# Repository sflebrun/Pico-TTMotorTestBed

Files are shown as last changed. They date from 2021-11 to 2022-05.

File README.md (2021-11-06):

# Pico-TTMotorTestBed
Environment and Code for testing two DC TT Gear Motors using a TB6612FNG Dual H-Bridge module and a Pico

## Build Environment
The code for ths project was developed using Visual Studio Code.  I see no reason why Thonny cannot be used with the code.

### Visual Studio Code modifications

* Add to the settings.json file the following line:<br/>
  "python.analysis.extraPaths:" ["./."]
  * This allows the editor to import from local files.
* Recommended (**Required**) Extensions:
  * MagicPython
  * **Pico-Go**
  * Pylance
  * Python

### Pico
The MicroPython UF2 file needs to be uploaded to the Pico.  This is the real program running on the Pico and it interrupts the
python code.  The three class files, ButtonInfo.py, MotorControl.py, and TTMotor.py must be uploaded to the Pico before the main
code, TTMotorTestBed.py, can run.

On multiple occasions, when trying to run the TTMotorTestBed python code, an error would occur that it could not find TTMotor.
Running the program again resolved this problem.  I do not know if this is a Pico issue or a Visual Studio Code/Pico-Go issue.

## Parts List
The links are places where I have bought the parts.  They are intended as recommendations and so you can 
identify the parts.

* [Raspberry Pi Pico](https://www.seeedstudio.com/Raspberry-Pi-Pico-p-4832.html)
* [TB6612FNG Dual H-Bridge](https://www.amazon.com/dp/B08J3S6G2N?psc=1&ref=ppx_yo2_dt_b_product_details&pldnSite=1)
* [2 TT Gear Motors with Wheels](https://smile.amazon.com/dp/B098Q1BCX5?psc=1&ref=ppx_yo2_dt_b_product_details)
* [Breadboard -- 830 points](https://smile.amazon.com/DEYUE-Solderless-Prototype-Breadboard-Points/dp/B07NVWR495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)
* [Dupont connector, male to male, various lengths](https://smile.amazon.com/Elegoo-EL-CP-004-Multicolored-Breadboard-arduino/dp/B01EV70C78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)
* [2 Breadboard Potentiometers](https://smile.amazon.com/dp/B09G9TBY38?psc=1&ref=ppx_yo2_dt_b_product_details)
* [3 Breadboard Push Buttons](https://smile.amazon.com/dp/B07XF3YMJ4?psc=1&ref=ppx_yo2_dt_b_product_details)
* 3D Printed Motor Stand [optional] See File: **Dual TT Gear Motor Test Bed.stl**
* 4 M3x30mm screws and nuts, if 3D Printed Motor Stand is used.

**Note** These are the parts that I used.  You can substitute most of the parts with something equivalent.  If you substitute a different
microcontroller board for the Pico or another Dual H-Bridge module for the TB6612FNG, changes to the code will be necessary.  For the Dual
H-Bridge Module see the comment about the Standby Pin in the MotorControl.py file.

## 3D Printed Parts
There is only one part that needs to be 3D printed.  That is the **Dual TT Motor Test Bed.stl**.  This can be printed with PLA filament with layers
set to 0.2mm and 20% infill.  No supports are necessary.  My printer is an Ender 3 Pro and the test bed had to be rotated 45 degrees so that the
test bed would fit in the 220mm x 220mm build area.

The TT Gear Motors mount on the pair of walls and requires M3 screws with nuts.  I recommend 30mm length screws. The screws pass through two walls
that are 25mm apart measured by the outside of each wall.  A 26mm length screw might work though it may not have enough thread sticking out to hold
the nut securely.

The Cad file for the TT Gear Motor Mount is included as **TestBedForTwoMotorsV3.FCStd**.  This file is a FreeCad file.

## The Code

### The Main Python Program

The main file, that contains the infinite loop, is **TTMotorTestBed.py**.  I ran this program thought the Pico directly from Visual Studio Code.
Clicking the ***Run*** button on the lower status line causes VS Code to upload the file and run it.  The extension ***Pico-Go*** provides the Run and upload 
buttons on the GUI.  This method of running the code means that I manually started and stopped running the Python code.

If the file **TTMotorTestBed.py** is renamed to **main.py** and uploaded to the Pico, the MicroPython interrupter program will automatically read and
run it everytime the Pico is powered up.

### Interrupt Handling

There are two push buttons used to toggle the directions of the motors.  One button per motor.  The code uses interrupts to handle the button being pushed.
Multiple issues had to be handled during the development of the code.  The first was button bounce and the other was that the Pico does not handle 
interrupts immediate and schedules them to be processed.

#### Debouncing

When a push button is pressed and released, it seldoms makes and breaks the connection cleanly.  Instead, the signal received from the pin may have a 
series of rises and falls in a small window of time as the connection is made and broken.  This is  called bounce.

There are two ways to handle debouncing: hardware solutions and software solutions.  The hardware solution is the better of the two solutions and 
should be used in production level electronics.  The con of this method is that it adds more components to the breadboard in a capacitor and a couple 
of resisters per button.  The software solution usually involves examining the button over a small window of time until it stablizes.  The con of
this solution is that if you make your window too small, you get false readings.

Because this is a one-off project and built on a single breadboard, I choose to use a software solution.  An additional factor needed to be considered
with my software solution [See the function ***buttonDebounce()*** in **TTMotorTestBed.py**].  The problem is that bounce can occur on both the push 
and release of a button.  The interrupt is only intended to trigger a direction toggle on the push or rising edge of the signal.  To over come the
fact that the falling edge can bounce and therefore look like another rising edge, the debounce function ignores the state of the button pin.
Instead, it looks for the state to remain the same over a specified period of time.  Once the button has stablized, the final state of the button
is used.  If the pin value is High, the interrupt function handles the interrupt.  If the final state is low, the interrupt ignores the interrupt.

#### Delayed Interrupt Handling

Normally when writing an interrupt handler, two things are considered.  The fist is to keep the interrupt handler as short, timewise, as possible.
The second is to disable additional interrupts for the same event from occurring while the first interrupt is being handled.  On the Pico, it is
not possible to prevent multiple interrupts from occurring with the same event.  In the case of the push button with bounce, each time the signal
rises another interrupt is generated.  In other words, multiple interrupts can be generated due to button bounce in the time between the first
interrupt occurs and when it is handled.  Disabling new interrupts during the processing of the interrupt handle fails to work in this case because
the extra interrupts have already occurred.

The debounce function handles most of the cases of multiple interrupts.  The one exception is if the button is held down for a long enough period
of time and multiple interrupts are queued for processing.  In this case, the interrupt handler processes the first interrupt and the pin value is HIGH.  When 
the second interrupt is handled, the interrupt handler finds that the button value is still HIGH and treats it as a new interrupt.  This case is 
resolved in the code by requiring a second interrupt that detects the release of the button.  Only one rising interrupt will be processed until a
matching falling interrupt is detected.  So if there are multiple rising or button pressed interrupts detected, all secondary interrupts are ignored 
until the button is released and the falling interrupt is detected.

* [See Interrupt Handling Problem in Pico -- Raspberry Pi Forums](https://forums.raspberrypi.com/viewtopic.php?t=319655) for more details.

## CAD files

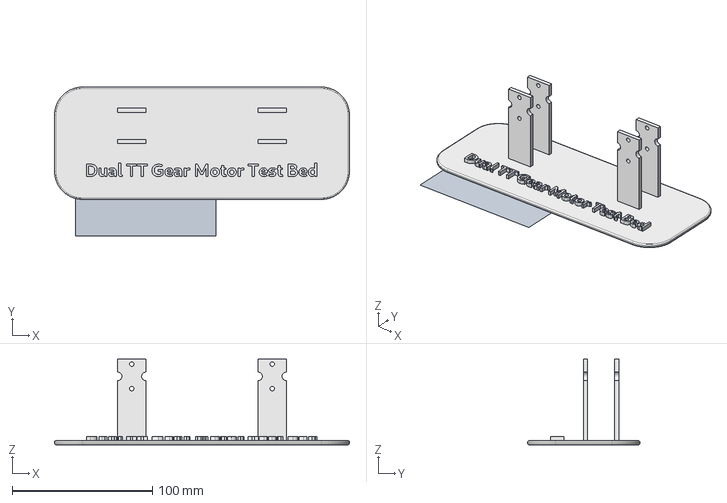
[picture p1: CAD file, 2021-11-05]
3D Models/TestBedForTwoMotorsV3.FCStd
210.0 x 106.0 x 61.0 mm
WPProxy
Dual TT Gear Motor Test Bed

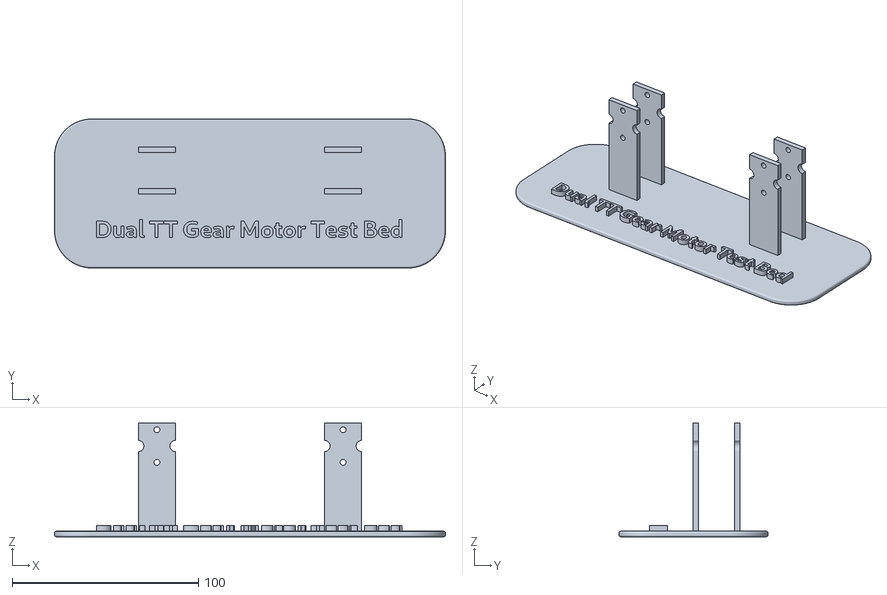
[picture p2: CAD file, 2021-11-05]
3D Models/Dual TT Gear Motor Test Bed.stl
210.0 x 80.0 x 61.0

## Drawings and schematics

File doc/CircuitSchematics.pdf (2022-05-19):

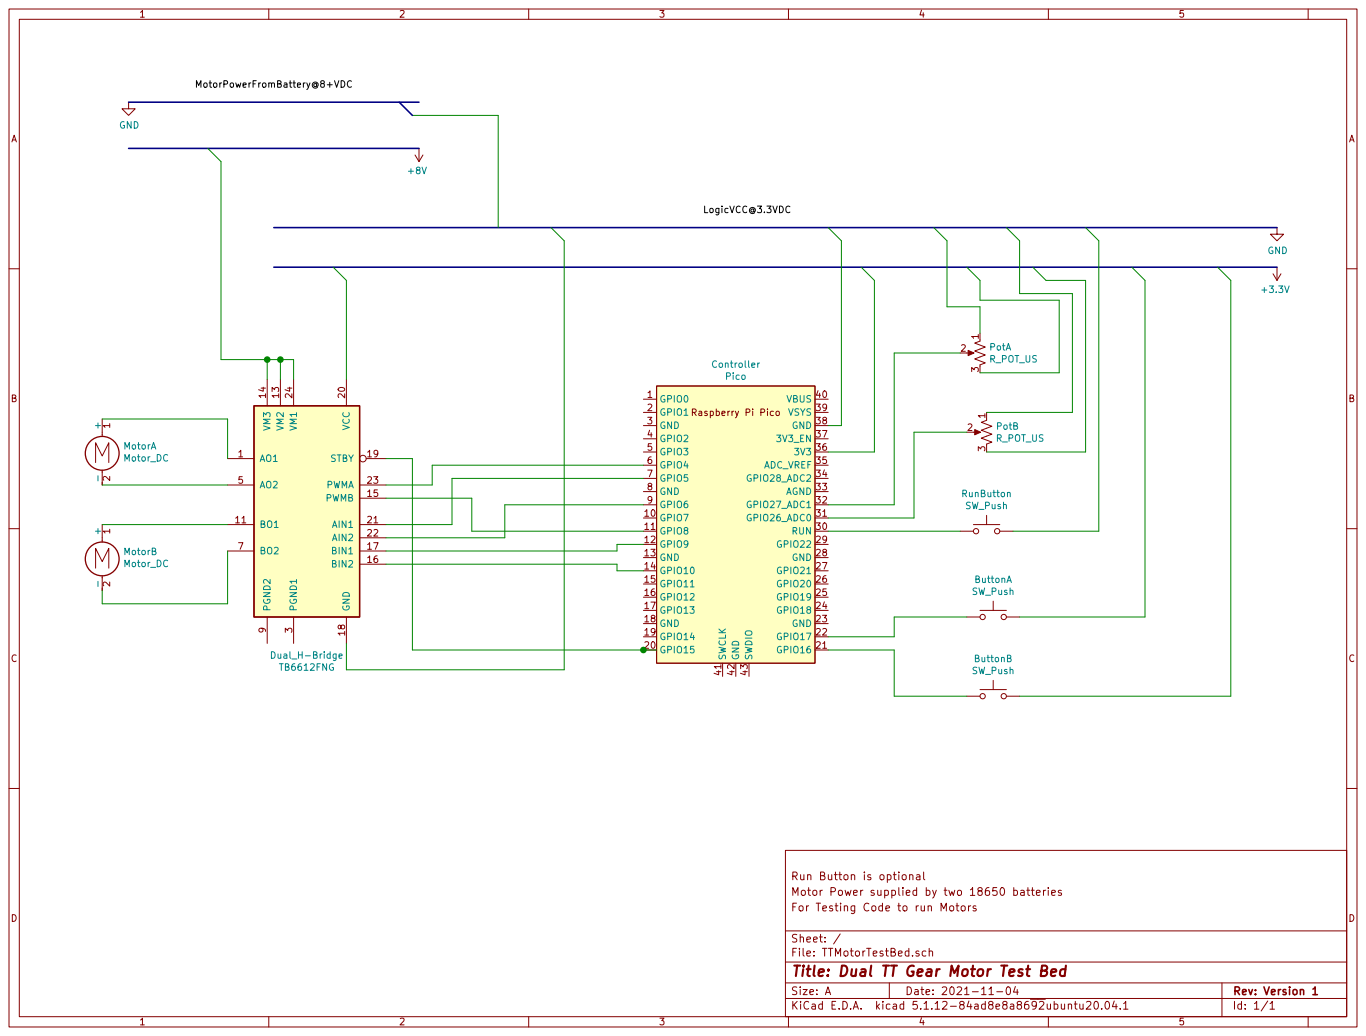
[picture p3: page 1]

3 PotB R_POT_US Raspberry Pi Pico GPIO0 1 GPIO7 10 GPIO8 11 GPIO9 12 GND 13 GPIO10 14 GPIO11 15 GPIO12 16 GPIO13 17 GND 18 GPIO14 19 GPIO1 2 GPIO15 20 GPIO16 21 GPIO17 22 GND 23 GPIO18 24 GPIO19 25 GPIO20 26 GPIO21 27 GND 28 GPIO22 29 GND 3 RUN 30 GPIO26_ADC0 31 GPIO27_ADC1 32 AGND 33 GPIO28_ADC2 34 ADC_VREF 35

Run Button is optional
Motor Power supplied by two 18650 batteries
File: TTMotorTestBed.sch Sheet: / For Testing Code to run Motors

Id: 1/1 Title: Dual TT Gear Motor Test Bed

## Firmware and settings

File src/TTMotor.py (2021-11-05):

# Defines the class that represents one motor part of TB6612FNG Dual H-Bridge.
#
# Note: This class is actually independent of what type of DC Motor is attached to 
#       the Dual H-Bridge Module.  My test setup is for a pair of TT Gear Motors,
#       hence the name.
#
# Three pins control each motor -- PMW, IN1, and IN2.  
#
# Motors are labeled A and B on the H-Bridge module.  This class only deals with
# a single motor so the A and B labels are ignored.  See the MotorControl class 
# for dealing with both motors and the Standby Pin.

from machine import Pin, PWM

# This class represents the part of the Dual H-Bridge module.
class TTMotor:
    """A Class that contains the state of a DC Motor, primarily for TT Gearbox Motors"""

    # Constants that denote motor direction.
    # Should be constants but Python const() does not appear to work in MicroPython
    # Please do no change these variables.
    STOPPED   = 0
    FORWARD   = 1
    BACKWARD  = 2

    # Default Constructor
    #    Current Direction is none or STOPPED
    #    Next Direction is FORWARD (by setting previous Direction to BACKWARD)
    #
    # @param  gpioPWM   The GPIO Pin Number, not the physical pin number, of the
    #                   pin used to set the motor speed with a pulse width modulation
    # @param  gpioIN1   The GPIO Pin Number used to determine direction of motor in
    #                   conjunction with gpioIN2
    # @param  gpioIN2   The GPIO Pin Number used to determine direction of motor in
    #                    conjunction with gpioIN1
    #
    def __init__(self, gpioPWM: int, gpioIN1: int, gpioIN2: int ):
        self.gpioPWM = gpioPWM
        self.gpioIN1 = gpioIN1
        self.gpioIN2 = gpioIN2
        self.motorSpeed  = 0
        self.IN1Value = False
        self.IN2Value = False

        if ( gpioPWM < 0 ):
            # Invalid value
            raise ValueError("TTMotor Constructor: Invalid GPIO PWM Pin number: " + str(gpioPWM))
        else:
            #Initialize the PWM pin
            self.pinPWM = Pin(gpioPWM, mode=Pin.OUT)

            self.pwmPin = PWM(self.pinPWM)
            self.pwmPin.freq(10000)  # 10kHz
            self.pwmPin.duty_u16(0)  # off

            # Initialize the two signal input pins
            self.in1    = Pin(gpioIN1, mode=Pin.OUT)
            self.in2    = Pin(gpioIN2, mode=Pin.OUT)

            self.in1.low()
            self.in2.low()

        self.currentDirection  = self.STOPPED
        self.previousDirection = self.BACKWARD

 
    # Determine if Pin ID is one of the GPIO Pins associated with this motor
    def usesPin( self, pinID: int ):
        if ( pinID == self.gpioPWM or pinID == self.gpioIN1 or pinID == self.gpioIN2 ):
            return True
        else:
            return False
        


    # Return the configured GPIO Pin object
    def pwm(self):
        return self.gpioPWM

    # Returns the GPIO Pin object for IN1
    def signal1Pin(self):
        return self.in1

    # Returns the GPIO Pin object for IN2
    def signal2Pin(self):
        return self.in2

    # Returns what the IN1 Pin should be set to: True == HIGH, False == LOW
    def signal1(self):
        return self.IN1Value

    # Returns what the IN2 Pin should be set to: True == HIGH, False == LOW
    def signal2(self):
        return self.IN2Value

    # Returns the Current Direction
    def direction(self):
        return self.currentDirection

    # Returns what the current speed is set to
    def speed(self):
        return self.motorSpeed
     
    # Returns the Next Direction
    #
    # The the toggle sequence is FORWARD --> STOPPED --> BACKWARD --> STOPPED --> repeat
    # So the next direction refers to the next N0N-Stopped direction.
    def nextDirection(self):
        if ( self.previousDirection == self.BACKWARD ):
            return self.FORWARD
        else:
            # all other values for Previous Direction leads to 
            return self.BACKWARD

    # Change direction based on the last none-stopped direction
    # Toggle Cycle:  FORWARD --> STOPPED --> BACKWARD --> STOPPED --> repeat
    def toggleDirection(self):
        if ( self.currentDirection == self.STOPPED ):
            # If currect direction is STOPPED, use the previous (non-STOPPED) direction
            # to determine the new current direction.
            if ( self.previousDirection == self.BACKWARD ):
                self.currentDirection = self.FORWARD
            else:
                self.currentDirection = self.BACKWARD
        else:
            # If current direction is FORWARD or BACKWARD, new current direction is STOPPED
            # and new previous direction is set to the old current direction
            self.previousDirection = self.currentDirection
            self.currentDirection  = self.STOPPED

    # Set actual Motor Speed and Direction
    #
    # This function actually writes to the Dual H-Bridge module, hence causing the motors to 
    # turn or to stop.
    def  motorControl( self, speed ):
        signal1 = False
        signal2 = False

        # Set Motor Speed to the passed value which may not match the zero speed of STOPPED
        # but it does match the Potentiometer that determines the moving speeds.
        self.motorSpeed = speed

        #print("Current Direction = ", self.currentDirection)
        if ( self.currentDirection == self.FORWARD ):
            signal2 = True
        elif ( self.currentDirection == self.BACKWARD ):
            signal1 = True
        else:
            speed = 0

        # Set Direction: STOPPED, FORWARD, or BACKWARD
        self.IN1Value = signal1
        if ( signal1 ):
            self.in1.on()
        else:
            self.in1.off()

        self.IN2Value = signal2
        if ( signal2 ):
            self.in2.on()
        else:
            self.in2.off()

        ## Set Speed
        self.pwmPin.duty_u16(speed)

        # End of MotorControl()


        
        

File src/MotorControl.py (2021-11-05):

# Class to handle two motors on a single TB6612FNG Dual H-Bridge module
# plus the extra control pins on the module, namely the STANDBY Pin.
#



from machine import Pin

import TTMotor

# The TB6612FNG Dual H-Bridge control class.
#
# The addition of the Standby Pin makes this class specific to the
# TB6612FNG module.  Removing all references to the Standby Pin would
# make this a generic Dual H-Bridge Controller class
#
class MotorControl:
    """Class to manage two TTMotor objects connected to the same
    TB6612FN Dual MOSFET H-Bridge module."""

    # Primary Constructor for this Class
    #
    # Note: It is the responsibility of the caller to have already created
    #       TTMotor objects for each of the two motors.  Only one motor is
    #       actually required if two motors are not connected to the H-Bridge.
    #
    # @param standby  The GPIO Pin Number, not the physical pin number, of the
    #                 pin used to control the StandBy pin on the TB6612FNG module.
    #
    # @param frontMotor  The TTMotor object for the motor that is considered to be
    #                    at the front of the car.
    #
    # @param backMotor   The TTMotor object for the motor that is considered to be
    #                    at the back of the car.
    #
    # @param flag        A boolean flag that denotes if True that the motors turn CW 
    #                    (Clockwise) when moving forward and if False that the motors
    #                    turn CCW (Counter Clockwise) when moving forward. 
    #                    NOT IMPLEMENTED YET -- Might be implemented when using four
    #                    motors and two TB6612FNG Dual H-Bridge modules.
    def __init__( self, standby: int, frontMotor=None, backMotor=None):
        self.gpioSTANDBY = standby
        self.pinSTANDBY  = Pin( self.gpioSTANDBY, mode=Pin.OUT )
        self.motors      = {}

        # Offsets for the Front and Back Motors in the motors array
        self.FRONT = 1
        self.BACK  = 2

        if ( frontMotor != None ):
            self.motors[self.FRONT] = frontMotor

        if ( backMotor != None ):
            self.motors[self.BACK]  = backMotor

        self.pinSTANDBY.high()

    # There is no general way to obtain the ID used to create a Pin object
    # after it has been created.  The following is a HACK, that assumes that
    # when a Pin object is converted to a string "Pin(xx, yy==zz, gg=pp)"
    # that the first parameter after the "(" starts in offset [4] and 
    # ends with a comma.
    def getPinID( self, pin ):
        pinString = str(pin)
        pinData   = pinString[4:-1].split(",")
        return int(pinData[0])


    # Modify speed being written to the each of the wheels
    # Either use speed or {frontSpeed and backSpeed}
    # If either frontSpeed or backSpeed are set to 0 or greater, those speeds
    # are used for each motor.  If they are not set, speed is used.  If none
    # of them are set, the speed used is 0.
    #
    # NOTE: This will result in data being written to the H-Bridge module and
    #       the motors to physically change speed.
    #
    def changeSpeed( self, speed=-1, frontSpeed=-1, backSpeed=-1):
        # Determining actual speeds based on which speed parameters are set or
        # in are their default values.
        if ( speed < 0 ):
            speed = 0

        if ( frontSpeed < 0 ):
            frontSpeed = speed

        if ( backSpeed < 0 ):
            backSpeed = speed

        # Make sure speeds are not greater than maximum value: 0xFFFF == 65535
        frontSpeed = frontSpeed & 0xFFFF
        backSpeed  = backSpeed  & 0xFFFF

        # change Motor Speeds
        #
        # NOTE: If TTMotor object was None, the if statements will evaluate to False
        if ( self.FRONT in self.motors.keys() ):
            self.motors[self.FRONT].motorControl(frontSpeed)

        if ( self.BACK  in self.motors.keys() ):
            self.motors[self.BACK].motorControl(backSpeed)


    # Toggle the direction the motor should turn based on Pin Number
    def toggleDirection(self, gpioPWM: int ):
        print("Toggle Direction on PWM Motor: ", gpioPWM)

        # Loop through motors array and toggle the direction on the appropriate motor
        for motor in self.motors.values():
            if ( motor.usesPin( gpioPWM ) ):
                motor.toggleDirection()
                print("Toggle Direction: Motor ID: ", gpioPWM, ", Direction = ", motor.direction())
        

    #
    # End of MotorControl class
    #

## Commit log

2021-11-05 Add files via upload
    The PDF is the schematic drawing of my setup. The stl and FCStd are the 3D model for the stand that holds the two motors. Initial checkin.
    [Dual TT Gear Motor Test Bed.stl, TestBedForTwoMotorsV3.FCStd]
2021-11-05 Add files via upload
    Initial checkin for source code. Note: TTMotorTestBed.py is the main program file. It can be run manually or renamed to main.py, loaded onto the Pico, and run automatically when the Pico powers up.
2021-11-05 Add files via upload
    Missed a file during initial commit. This file contains the class that manages a single DC Motor that is connected through a Dual H-Bridge module.
    [TTMotor.py]
2021-11-05 Added second interrupt handler. The original handler is for rising signal interrupts which occur when a button is pressed. The new handler is for falling signal interrupts which occur when a button i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
    The new behavior is that once a pressed button interrupt has been handled, the code will ignore all other pressed interrupts
    until a released button interrupt has occurred. There is bounce occurring when the button is pressed and released. This
    prevents secondary pressed button interrupts that occur after the first one is detected and before the first one is processed
    from triggering false detection. Again this is due to bounce and the fact that the Pico does not process an interr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
    [ButtonInfo.py, TTMotorTestBed.py]
2021-11-05 Moved files into subdirectories for Documentation, 3D Printing, and Source
    [Dual TT Gear Motor Test Bed.stl, TestBedForTwoMotorsV3.FCStd]
2021-11-06 Changed the name of TTMotorTestBed.pdf to CircuitSchematics.pdf in order for the file name to better represent its content.
2021-11-06 Turns out that MicroPython does not support multiple interrupt handlers for the same object. Each time, an interrupt is setup, the previous interrupt handler is dropped in favor of the new one.
    Replaced the two interrupt handlers, buttonPressedHandler() and
    buttonReleasedHandler(), with a single interrupt handler,
    buttonHandler(), that does the job of both of the older handlers.
    [TTMotorTestBed.py]
2022-05-19 Fixed wires connecting H-Bridge module to Pico. The old wires missed the pins on the H-Bridge module in the schematic diagram.
